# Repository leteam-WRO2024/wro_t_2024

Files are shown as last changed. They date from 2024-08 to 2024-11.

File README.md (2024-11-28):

# Engineering materials

This repository contains engineering materials of "yatta-team (Leteam)" self-driven vehicle's model participating in the WRO Future Engineers competition in the season 2024.

## Content

-   `t-photos` contains photos of the team
-   `v-photos` contains photos of the vehicle
-   `video` contains the video.md file with the link to a video where driving demonstration exists
-   `schemes` contains diagrams about the design and cricut
-   `src` contains the source code that is used
-   `chasis` contains photos of the used chasis and its parts

**AS OF THIS COMMIT IT ONLY CONTAINS THE SOURCE**

## Hardware

| HARDWARE PARTS | References |
| --- | --- |
| Chasis | [4WDRC Chassis S3003 Servo](https://www.elecrow.com/4wd-smart-car-robot-chassis-for-arduino-servo-steering.html) |
| Servo | [S3003 FUTABA SERVO](https://www.es.co.th/schemetic/pdf/et-servo-s3003.pdf) |
| Main-Controller | [RPI-5](https://www.raspberrypi.com/products/raspberry-pi-5/) |
| Secondry-Controller | [Arduino ATmega328p (Arduino Nano 3.x)](https://store.arduino.cc/products/arduino-nano) |
| gyroscope | [BNO085](https://www.ceva-ip.com/wp-content/uploads/2019/10/BNO080_085-Datasheet.pdf) |
| Camera | [usb 170 degree fisheye cam](https://www.amazon.com/ALPCAM-Camera-Module-Webcam-Fisheye/dp/B07VVH39DC/) |
| Other-Parts | Ultrasonics, full-bridge, Voltage regulator, green-light, button |

# Software

We are using the rasberry-pi-4 as a the main controller // computer.
We also use the arduino ATmega328p to - read the Ultrasonic sensors -> filter the readings -> send them using the serial connection to rpi

## Code basic idea

We took advantage of our rasberry pi ability to run multiple processes at the same time so we devided the main program into seperate threads

### MAIN-THREAD

In the main thread we run all the other threads while waiting for the mpu6050 to calibrate, then the main thread waits for a button click after the calibration is finished, our main thread continous to start the car movment by calling the moving function and turning function when needed

---

When the MPU-THREAD finishes calibration and the current angle is set to 0, the main thread waits for a button click.

if the button is clicked the main thread starts the car moving function.

### MPU-THREAD

In the MPU thread we run a function that calculates all the possible angles and calibrates the gyroscope to the current position and then it runs a while loop the gets the current angle by storing it in a class attribute.

-   This thread is a BLOCKING thread, because it blocks the execution of the main thread and that is needed to make the gyroscope calibrate correctly since the gyro we have can not save old calibration like other gyroscopes.

-   The main thread is blocked by a while loop that waits for the current angle to change from -1 to anything else (in this case it should be 0 because after the calibration of the mpu6050 the first angle is set to 0)

-   This thread then keeps running and reading the new angle and setting it to the current angle

-   Events -> None

### DISTANCE-THREAD

In the DISTANCE thread we run a loop that reads the serial continuously, when the arduino finishes reading the ultrasonics, it sends the data throught the serial and the rasberry pi throught this thread it reads and updates the distances.

-   Events -> stop_event which is called at the exit of the program to free and make sure the memory is clean to help pythons garbage collector and stop any overflows

### COLOR-THREAD - direction detection

In the COLOR thread we start reading frames from the camera and do some python and opencv processing on the frames and check for orange and blue colors ... if blue is found then it sets the turn direction to 1 else if orange is found it sets the turn direction to -1 else if orange nor blue were found then turn based on the left or right distance

-> direction-detection chart:
process camera frames -> blue is found <-> direction = 1 <-> else if orange is found <-> direction = -1 <-> else orange nor blue were found -> read left and right distance -> if left is bigger -> direction = 1 <-> else if right is bigger <-> direction = -1

-   Events -> stop_event which stops the thread in a certain case is met and when the program exits

## Turning:

Using ultrasonic sensors (sonar sensors) we check for the right, left, and front distances then we use certain conditions in the moving function that tells the robot to turn based on the direction that was defined by the [COLOR-THREAD](#color-thread---direction-detection).

The turning mechanism uses the mpu6050 to read the current angle and the desired angle to make the robot turn 90 degrees (somewhat exactly ...)

## Avoiding Walls:

Using the right, left distances from the ultrasonics, we calculate a distance error based on a threshold value, then we use a PID algorithm and get a negative or positive return value based on the error ...

After that we use the desired angle (the heading angle e.g 90, 180, 270, 360 or (0)) and the current angle that the gyroscope is reading to calculate an angle error and with some maths we make the robot get the required servo angle to make it go in a 90 degree straight path

we sum the values e.g if the distance error was negative then it helps go away from the right wall, otherwise if positive it helps go away from the left wall, while keeping the angle straight

In the last code, we replaced the readings from ultrasonic sensors with the x values of the black color contours on the right and left sides of the cropped image.

## 3 LAPS detection

At first the robot only runs a for loop for each lap and a for loop inside of it for each corner, and runs the moving and turning functions inside, which works correctly but, we are aware its error prone, In the latest update, we handled each edge of the track with a dedicated function that identifies the end of the edge in the first round when it detects the black color in front of it. In the second round, it identifies the end by the color of the line on the floor, considering the possibility of seeing the black color on the sides while trying to avoid obstacles as the end of the path.

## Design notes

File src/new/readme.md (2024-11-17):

that folder contains our work after removing the ultrasonic sensor from our robot

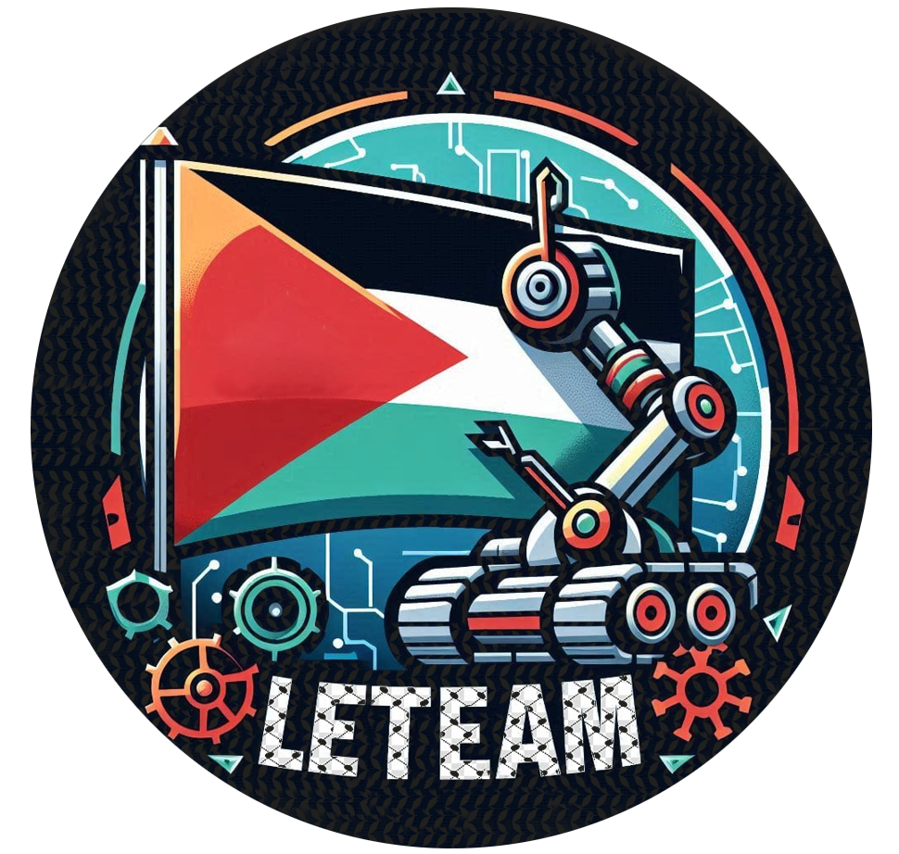
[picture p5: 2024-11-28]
leteam4(1).png

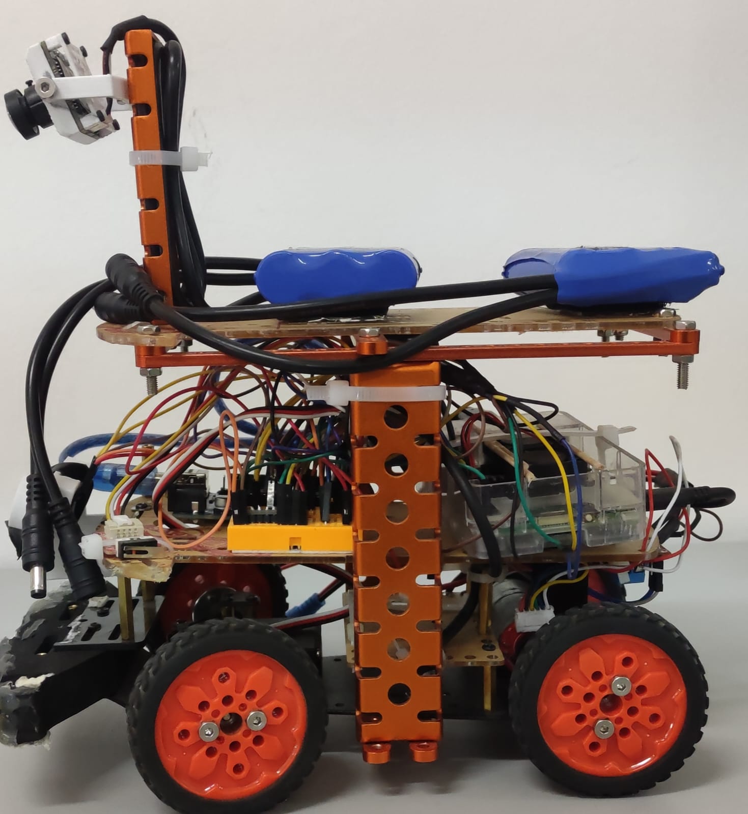
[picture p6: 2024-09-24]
v-photos/left.jpeg

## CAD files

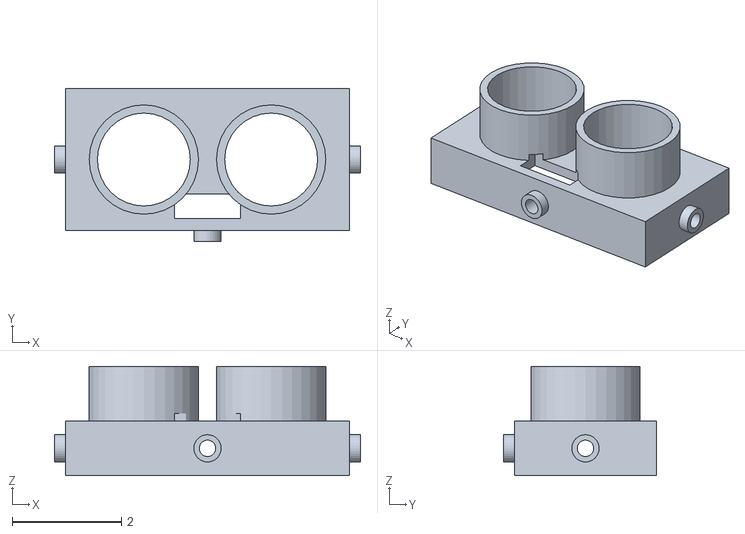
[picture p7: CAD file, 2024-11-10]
models/US100.stl
5.60 x 2.80 x 2.00

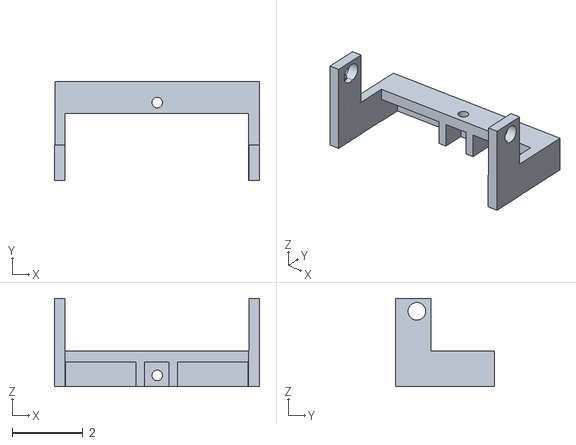
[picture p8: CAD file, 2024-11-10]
models/us100mount.stl
5.81 x 2.80 x 2.50

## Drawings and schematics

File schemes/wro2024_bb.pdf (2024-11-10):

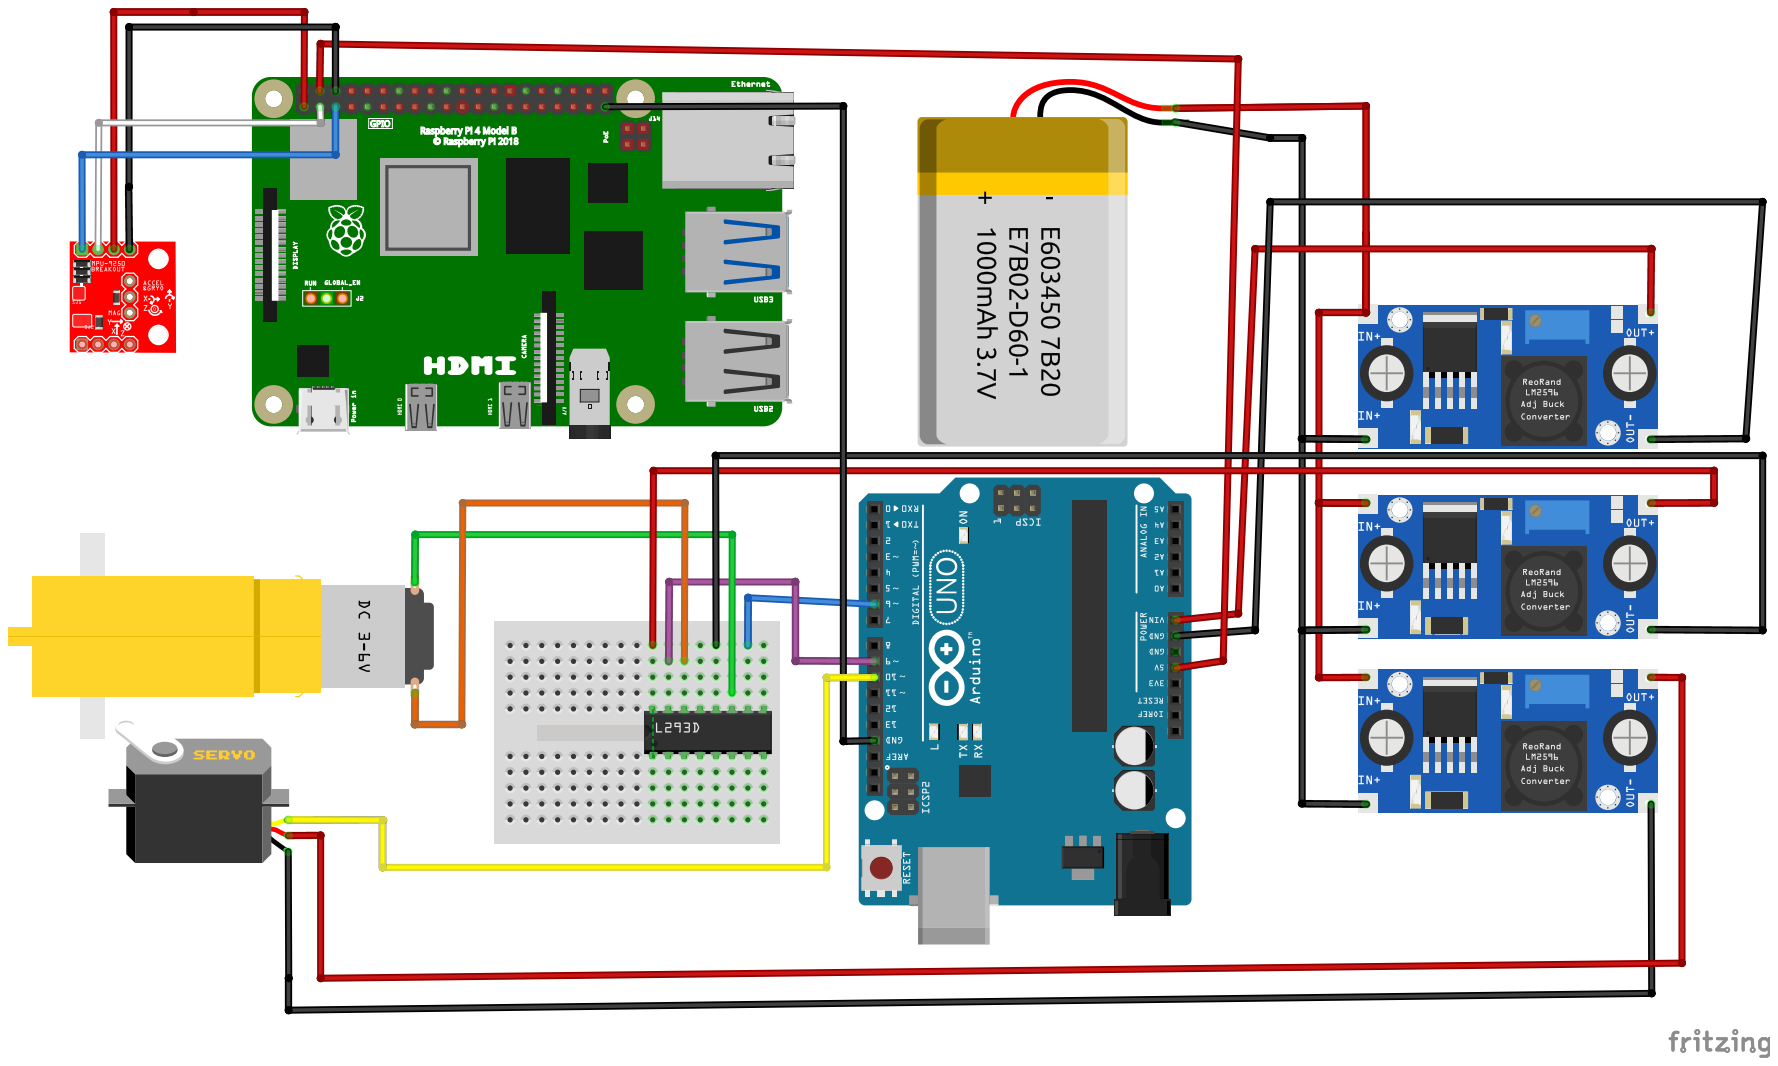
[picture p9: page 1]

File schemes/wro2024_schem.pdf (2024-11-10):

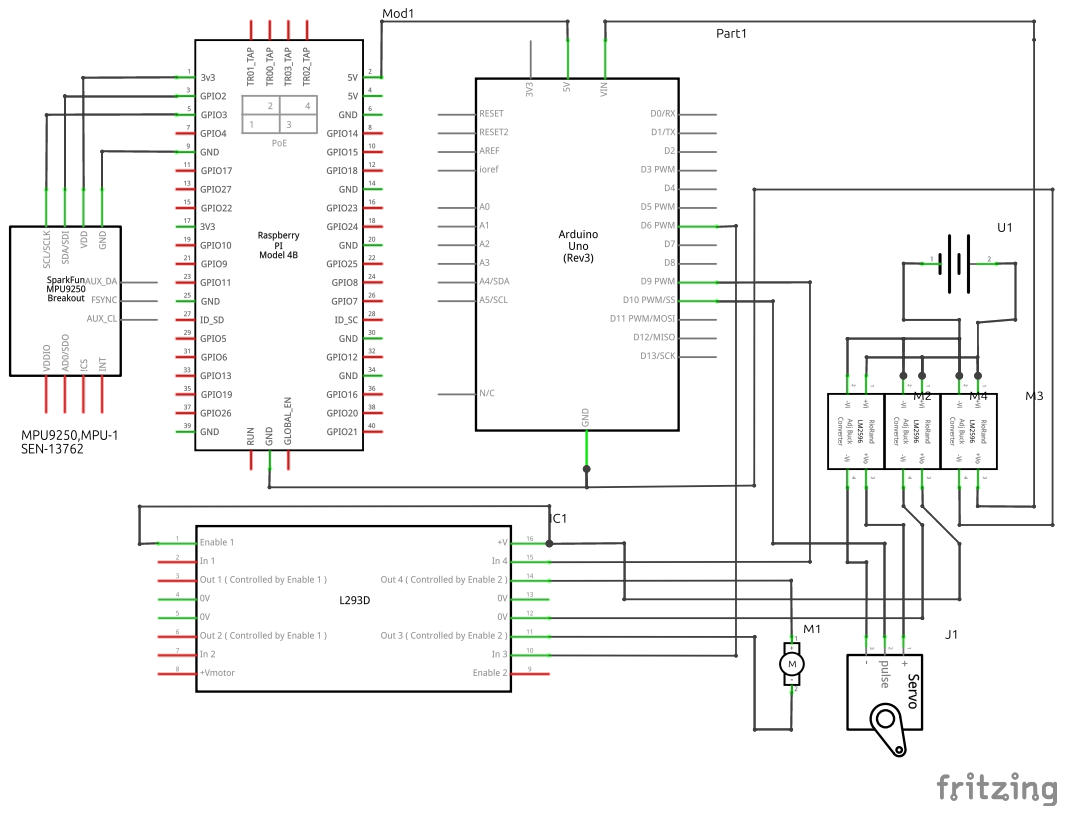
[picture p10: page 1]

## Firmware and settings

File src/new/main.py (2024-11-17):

import imutils
import time
import cv2
import numpy as np
from WebcamVideoStream import WebcamVideoStream as ws
from threading import Thread
from MyGyro import BNO085 as BN
from gpiozero import RotaryEncoder
from threading import Event
import RPi.GPIO as gpo
gpo.setmode(gpo.BCM)
from time import sleep
btn=6
gpo.setup(btn,gpo.IN)
import serial
#initialize arduino communications
ser = serial.Serial('/dev/ttyACM0', 2000000)
ser.flush()
first_Side=True
ser.reset_input_buffer()
time.sleep(2)
if not ser.is_open:
    ser.open()
    time.sleep(2)
#initialize Encoder
rotor = RotaryEncoder(19, 13, wrap=True, max_steps=18000)
rotor.steps = 0
done = Event()
CW=-1

def stop_script():
    print('Exiting')
    done.set()
    
#parameters
min_angle=30
mid_angle=90
max_angle=130
class ColorsCoordinations:

    # allow the camera to warmup
    x=y=w=h=-1
    g_l=[54,98,35]
    g_u=[86,255,255]
    b_l=[0,0,0]
    b_u=[255,255,30]
    bu_l=[110,85,100]
    bu_u=[125,255,255]
    r_l=[170,50,73]
    r_u=[180,255,255]
    o_l=[0,100,110]
    o_u=[50,255,255]
    #Ignore the warning message
    cam=ws()
    cam.start()
    xr=-1
    yr=-1
    xl=-1
    yl=-1
    yf=-1
    xo=-1
    xb=-1
    imu=BN()
    imu.start()
    def getcoor(self,imageFrame,l,u,name,delay,show,minsize):
        while True:

            hsv_frame2 = cv2.cvtColor(imageFrame, cv2.COLOR_BGR2HSV)
            kernal = np.ones((5, 5), "uint8") 
            dilated_frame = cv2.dilate(hsv_frame2, kernal)
            dilated_frame = cv2.erode(dilated_frame, kernal)

            lower = np.array([l[0], l[1], l[2]], np.uint8) 
            upper = np.array([u[0], u[1], u[2]], np.uint8) 
            mask = cv2.inRange(dilated_frame, lower, upper) 

            contours, _ = cv2.findContours(mask, cv2.RETR_TREE, cv2.CHAIN_APPROX_NONE)
            if len(contours)>0:
                c = max(contours, key = cv2.contourArea)
                area = cv2.contourArea(c)
                if(area > minsize):
                    cv2.drawContours(imageFrame, c, -1, (0, 255, 0), 2)
                    self.x, self.y, self.w, self.h = cv2.boundingRect(c)

        
            x=self.x 
            y=self.y
            w=self.w
            h=self.h
            self.x=self.y=-1
            if show:
                cv2.imshow(name,imageFrame)
                key = cv2.waitKey(delay) & 0xFF
            return x,y,w,h
    def boarders(self,delay,show):
        frame=self.cam.read()
        #print(frame.shape)
        #frame1=frame
        frame1=frame[420:450,0:400]
        frame2=frame[420:450,400:800]
        #show fps
        '''
        nframe=time.time()
        fps=1/(nframe-pframe)
        pframe=nframe
        fps=int(fps)
        fps=str(fps)
        cv2.putText(frame2,fps,(7,25),cv2.FONT_HERSHEY_SIMPLEX,1,(255,255,255),1,cv2.LINE_AA)
        '''
        xl, self.yl, lw, lh=c.getcoor(frame1,c.b_l,c.b_u,"f1",delay,show,300)
        
        if xl != -1:
            self.xl = (xl + lw) // 2
        else:
            self.xl = -1
        
        self.xr, self.yr, rw, rh=c.getcoor(frame2,c.b_l,c.b_u,"f2",delay,show,300)
        
    def front(self,delay,show,heading):
        frame=self.cam.read()

        curr=self.imu.Read_Yaw()
        while curr=='err':
            curr=self.imu.Read_Yaw()
        diff=heading-curr
        #print(diff)
        if diff>300:
            diff=360-diff
        elif diff<-300:
            diff=diff+360
            
        #print(diff)
        diff=int(diff)*4
        if diff>300:
            diff=300
        elif diff<-300:
            diff=-300
        
        frame3=frame[90:450,350+diff:450+diff]

        x3,y3,w,h=c.getcoor(frame3,c.b_l,c.b_u,"f3",delay,show,1000)
        #print(y3)
        self.yf=y3
    def ground(self,delay,show,heading):
        #pframe=time.time()
        frame=self.cam.read()


        
        frame3=frame[150:225,380:420]

        self.xb,y1,w,h=c.getcoor(frame3,c.bu_l,c.bu_u,"f_blue",delay,show,50)
        self.xo,y2,w,h=c.getcoor(frame3,c.o_l,c.o_u,"f_orange",delay,show,50)        
        


c=ColorsCoordinations()
frame=c.cam.read()

time.sleep(0.1)
pframe=0
nframe=0
show=False
delay=5
side_values=[]
def turn90_halfback():
    rotor.steps=0
    speed=200
    stop()
    roter_limmit=280
    go_left(speed)
    #while rotor.steps<roter_limmit:
        #ser.write(code.encode("utf-8"))
        #time.sleep(0.1)
    while  rotor.steps< roter_limmit:
        forward(speed)
    stop()

    go_right(speed)
    time.sleep(0.2)
    while  rotor.steps> roter_limmit:
        backward(speed)
    stop()
    time.sleep(0.2)
def turn90():
    rotor.steps=0
    speed=200
    stop()
    roter_limmit=470
    go_left(speed)
    #while rotor.steps<roter_limmit:
        #ser.write(code.encode("utf-8"))
        #time.sleep(0.1)
    while  rotor.steps< roter_limmit:
        forward(speed)
    stop()
def turn90c():
    rotor.steps=0
    speed=200
    stop()
    roter_limmit=470
    go_right(speed)
    #while rotor.steps<roter_limmit:
        #ser.write(code.encode("utf-8"))
        #time.sleep(0.1)
    while  rotor.steps< roter_limmit:
        forward(speed)
    stop()

def calculate_sides_values(first_side):
    side_values.append(first_side)
    for i in range(3):
        next_side_angle=side_values[i]+90
        if next_side_angle>360:
            next_side_angle=next_side_angle-360
        side_values.append(next_side_angle)
    print(side_values)
#communications with arduino test code
def forward(speed):
    code = f"f:{speed}$"    
    ser.write(code.encode("utf-8"))
def backward(speed):
    code = f"b:{speed}$"    
    ser.write(code.encode("utf-8"))
def stop():
    code = f"s: $"    
    ser.write(code.encode("utf-8"))
def set_servo_angle(angle):
    code = f"a:{angle}$"
    ser.write(code.encode("utf-8"))
def go_right(speed):
    set_servo_angle(max_angle)
    forward(speed)
def go_left(speed):
    print("am going left")
    set_servo_angle(min_angle)
    forward(speed)
def go_right_r(speed):
    set_servo_angle(min_angle)
    backward(speed)
def go_left_r(speed):
    set_servo_angle(max_angle)
    backward(speed)
def lastrun(side_angle):

    rotor.steps=0
    code = f"a:{mid_angle}$"
    ser.write(code.encode("utf-8"))
    speed=255
    while rotor.steps<500:
        speed_offset=0#int((rotor.steps/900)*80)
        speed=speed-speed_offset
        if speed<180:
            speed=180
        code = f"f:{speed}$"    
        ser.write(code.encode("utf-8"))
        err=0
        Gyro_angle=c.imu.Read_Yaw()
        if not Gyro_angle=="err":
            err=(side_angle-Gyro_angle)
            if err>100:
                err=360-err
            elif err<-100:
                err=err+360
        servo_angle=mid_angle+err
        code = f"a:{servo_angle}$"
        ser.write(code.encode("utf-8"))
        c.boarders(delay,show)
        
    code = f"s:{speed}$"    
    ser.write(code.encode("utf-8"))
    print(rotor.steps)
    
def onesidedrive(side_angle):
    global first_Side
    global CW
    c.front(delay,show,side_angle)
    roter_limit=1200
    if first_Side:
        first_Side=False
        roter_limit=50
    c.boarders(delay,show)
    rotor.steps=0
    yf=c.yf
    code = f"a:{mid_angle}$"
    ser.write(code.encode("utf-8"))
    speed=255
    ptime=time.time()
    while yf==-1 or rotor.steps<roter_limit:
        speed_offset=0#int((rotor.steps/900)*80)
        speed=speed-speed_offset
        if speed<180:
            speed=180
        code = f"f:{speed}$"    
        ser.write(code.encode("utf-8"))
        err = 0
        Gyro_angle = c.imu.Read_Yaw()
        
        dist_err = 0
        
        if c.xl > 70 and c.xl != -1:
            dist_err = -(70 - c.xl) * 15
        elif c.xr < 200 and c.xr != -1:
            #print("am here")
            dist_err = -(200 - c.xr) * 4
            
        if not Gyro_angle=="err":
            err=(side_angle-Gyro_angle)
            if err>100:
                err=360-err
            elif err<-100:
                err=err+360

        servo_angle = mid_angle + err + dist_err

        code = f"a:{servo_angle}$"
        ser.write(code.encode("utf-8"))
        c.boarders(delay,show)
        c.front(delay,show,side_angle)
        yf=c.yf
        ftime=time.time()
        fps=1/(ftime-ptime)
        ptime=ftime
        #print(f"fps: {fps} {c.xr}{c.xl}")
        
    code = f"s:{speed}$"    
    ser.write(code.encode("utf-8"))
    print(rotor.steps)
def ccw_run():

    for i in range(3):
        onesidedrive(side_values[0])
        turn90()
        onesidedrive(side_values[3])
        turn90()
        onesidedrive(side_values[2])
        turn90()
        onesidedrive(side_values[1])
        turn90()
    lastrun(side_values[0])
    print(time.time()-t1)
    
def cw_run():

    for i in range(3):
        onesidedrive(side_values[0])
        turn90c()
        onesidedrive(side_values[1])
        turn90c()
        onesidedrive(side_values[2])
        turn90c()
        onesidedrive(side_values[3])
        turn90c()
    lastrun(side_values[0])
    print(time.time()-t1)
    
def firstsidedrive(side_angle):
    global first_Side
    global CW
    c.front(delay,show,side_angle)
    roter_limit=1200
    if first_Side:
        first_Side=False
        roter_limit=500
    c.boarders(delay,show)
    c.ground(delay,show,side_angle)
    rotor.steps=0
    yf=c.yf
    code = f"a:{mid_angle}$"
    ser.write(code.encode("utf-8"))
    speed=100
    ptime=time.time()
    while c.xo==-1 and c.xb==-1:
        c.ground(delay,show,side_angle)
        speed_offset=0#int((rotor.steps/900)*80)
        speed=speed-speed_offset
        if speed<180:
            speed=180
        code = f"f:{speed}$"    
        ser.write(code.encode("utf-8"))
        err=0
        Gyro_angle=c.imu.Read_Yaw()
 
        if not Gyro_angle=="err":
            err=(side_angle-Gyro_angle)
            if err>100:
                err=360-err
            elif err<-100:
                err=err+360
        print(f"err {err}")
        servo_angle=mid_angle+err
        code = f"a:{servo_angle}$"
        ser.write(code.encode("utf-8"))
        c.boarders(delay,show)
        c.front(delay,show,side_angle)
        yf=c.yf
        ftime=time.time()
        fps=1/(ftime-ptime)
        ptime=ftime
        #print(f"fps: {fps} {c.xr}{c.xl}")
    if c.xo==-1:
        print("CCW")
        CW=False
    else:
        print("CW")
        CW=True

    code = f"s:{speed}$"    
    ser.write(code.encode("utf-8"))
    print(rotor.steps)


while True:
    if not gpo.input(btn):
        time.sleep(1)
        t1=time.time()
        heading=c.imu.Read_Yaw()
        while heading=='err':
           heading=c.imu.Read_Yaw()
        calculate_sides_values(heading)



        firstsidedrive(heading)

        first_Side=True

        if CW:
            cw_run()
        else:
            print("am in ccw")
            ccw_run()

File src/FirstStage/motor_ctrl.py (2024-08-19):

from gpiozero import Motor, AngularServo
from gpiozero.pins.pigpio import PiGPIOFactory
from typing import Union, NewType
from time import sleep
from pid_ctrl import pidc


class mctrl():
    def __init__(self, motorPins: list, servoPin: int, speed: int = 1, debug: bool = False) -> None:
        self.motorPins: list = motorPins
        self.servoPin: int = servoPin

        # OLD pidc vals: 0.6, 0.0, 0.3 True
        self.motor: Motor = Motor(*self.motorPins)
        self.factory = PiGPIOFactory()
        self.servo = AngularServo(self.servoPin, min_angle=0, max_angle=180,min_pulse_width=0.0005, max_pulse_width=0.0025, pin_factory=self.factory)

        # 0.8789 0.04 0.048
        # self.pid = pidc(0.6, 0.038, 0.034, True)
        self.pid = pidc(0.9, 0, 0.02, True)

        self.distance_threshold = 25
        self.debug = debug

        self.__speed = speed
        self.__direction = 0

        self.min_angle = 60
        self.max_angle = 140
        self.mid_angle = 110
        
        self.turns = 0

    @property
    def angle(self):
        return self.servo.angle

    @angle.setter
    def angle(self, val):
        self.servo.angle = self.map_angle(val)

    @property
    def direction(self):
        return self.__direction

    @direction.setter
    def direction(self, val):
        if val not in [1, 0, -1]:
            self.__direction = 0
            print("Direction should be in [1, 0, -1] ... Resseting to 0")
        self.__direction = val

    @property
    def speed(self):
        return self.__speed

    @speed.setter
    def speed(self, val):
        self.__speed = round(min(1, max(0, val)), 2)

    def minfo(self, val):
        if self.debug:
            print(val)

    def get_next_angle(self, angle: Union[int, float], ninety_deg: bool = False):
        next_angle = ((angle + 10) + (self.direction * 90)) % 360
        if ninety_deg:
            next_angle = (round(next_angle / 90)) * 90

        return next_angle

    def get_heading_angle(self, angle: Union[float, int]):
        return (self.get_next_angle(angle, True) - (self.direction * 90)) % 360
    
    def get_current_turn(self, angle: Union[float, int]):
        if self.get_heading_angle(angle = angle) == 0:
            self.turns += 1
            
    def map_angle(self, angle: Union[int, float]):
        return max(self.min_angle, min(self.max_angle, angle))

    def adjust_angle(self, heading: Union[int, float], reading: Union[int, float], right_distance: Union[int, float], left_distance: Union[int, float]):


        if right_distance == 0:
            right_distance = 200
        if left_distance == 0:
            left_distance = 200
        
        distance_error = min(right_distance, 40) - min(left_distance, 40)
        
    
        error_val = reading - heading + distance_error
        error_val = ((error_val + 180) % 360) - 180
        self.angle = (error_val + self.mid_angle)

    def direction_turn(self):
        if self.direction == -1:
            self.turn_right()
        elif self.direction == 1:
            self.turn_left()

    # Needs more work i think never tested it fully
    def fix_forward(self, heading: Union[float, int] = 0, reading: Union[float, int] = 0, left_distance: Union[float, int] = 0, right_distance: Union[float, int] = 0):
        print("\n\n::::::::Inside fix, forward::::::::\n\n")

        if left_distance > right_distance:
            self.turn_right()
        elif right_distance > left_distance:
            self.turn_left()

        self.move_backward(nspeed=1)
        sleep(1)
        self.reverse_angle()
        self.move_forward(nspeed=0.8)
        sleep(0.84)
        for _ in range(3):
            self.adjust_angle(heading, reading, left_distance, right_distance)
            sleep(0.005)

    def fix_stuck(self, heading: Union[float, int] = 0, reading: Union[float, int] = 0, left_distance: Union[float, int] = 0, right_distance: Union[float, int] = 0):
        self.stop_car()
        self.reverse_angle()
        self.move_backward(nspeed=1)
        sleep(1)
        self.reverse_angle()
        self.move_forward()

    def reverse_angle(self):
        self.angle = (self.mid_angle - self.angle) + self.mid_angle

    def turn_forward(self):
        self.angle = self.mid_angle

    def turn_left(self):
        self.angle = self.min_angle

    def turn_right(self):
        self.angle = self.max_angle

    def move_forward(self, nspeed: Union[int, float]  = 0):
        self.motor.forward(nspeed if nspeed else self.speed)

    def move_backward(self, nspeed: Union[int, float] = 0):
        self.motor.backward(nspeed if nspeed else self.speed)

    def stop_car(self):
        self.motor.stop()

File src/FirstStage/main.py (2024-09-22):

from ultrasonic_ctrl import ultra
from mpu_ctrl import MPU
from encoder import Encoder
from gpiozero import Button, LED
from motor_ctrl import mctrl
from time import sleep, time
from threading import Thread, Event
from ColorCoords import ColorsCoordinations
import cv2
import numpy as np

new_J = 0
COLOR_RANGES = {
    "green":    (np.array([55, 173, 35], np.uint8), np.array([90, 255, 205], np.uint8)),
    "red":      (np.array([0, 51, 64], np.uint8), np.array([180, 255, 255], np.uint8)),
    "orange":   (np.array([2, 40, 60], np.uint8), np.array([30, 255, 255], np.uint8)),
    "blue":     (np.array([90, 105, 90], np.uint8), np.array([125, 255, 255], np.uint8))
}

def read_ultra(event: Event):
    while not event.is_set():
        frontUltra.distance = frontUltra.calcDistance()
        leftUltra.distance = leftUltra.calcDistance()
        rightUltra.distance = rightUltra.calcDistance()

def mpu_loop(mpu: MPU):
    global new_J
    mpu.setUp()
    mpu.calibrateGyro(500)

    while True:
        try:
            mpu.currentAngle = mpu.compFilter(1) + ((3 * new_J) * motors.direction)
            # mpu.currentAngle = mpu.compFilter(1)
            sleep(0.000007)
        except:
            
            pass

def get_color(event: Event):
    motors.direction = 0
    while not event.is_set():
        orange = color_reco.detect_color("orange")
        blue = color_reco.detect_color("blue")
        if orange != (-1, -1):
            motors.direction = -1
        elif blue != (-1, -1):
            motors.direction = 1

        if motors.direction != 0:
            event.set()
            color_reco.stop = True
        # print(f"direction: {motors.direction}")


def starting_point_adjustment():
    heading = motors.get_heading_angle(mpu.currentAngle)
    motors.move_forward(0.7)


    if frontUltra == 0:
        sleep(1)
    elif frontUltra > 145:
        while (frontUltra > 145 or frontUltra == 0):
            pass
        # motors.adjust_angle(heading, mpu.currentAngle, rightUltra, leftUltra)
            # print("adjusting")
    print("out")

    motors.stop_car()
    motors.turn_forward()


def moveUntilDist():
    heading = motors.get_heading_angle(mpu.currentAngle)
    motors.adjust_angle(heading, mpu.currentAngle, rightUltra, leftUltra)

    motors.move_forward()

    motors.minfo(f"\n\nFRONT:: {frontUltra}\n\n")
    while True:
            # print(f"Moving with speed {motors.speed}  --- front {frontUltra}")
        if (frontUltra < 82 and frontUltra != 0) or (leftUltra > 120 or rightUltra > 120):
            break
        motors.adjust_angle(heading, mpu.currentAngle, rightUltra, leftUltra)
                
        motors.minfo(
            f"\nFRONT:: {frontUltra}\nRIGHT:: {rightUltra}\nLEFT:: {leftUltra}\n")

    print("OUT OF LOOP")
    motors.turn_forward()
    motors.stop_car()
    motors.speed = 1
    
def turn():

    heading = motors.get_heading_angle(mpu.currentAngle)

    mpu.nextAngle = motors.get_next_angle(heading, True)
    motors.direction_turn()
    sleep(0.003)
     
    motors.move_forward(1)

    mpu.dinfo(
        f"ABOVE:: ({mpu.currentAngle} - {mpu.nextAngle}) * {motors.direction} = {(mpu.nextAngle - mpu.currentAngle) * motors.direction}")
    
    while not (250 > (mpu.currentAngle - mpu.nextAngle) * motors.direction >= -5):
        mpu.dinfo(
            f"({mpu.currentAngle} - {mpu.nextAngle}) * {motors.direction} = {(mpu.nextAngle - mpu.currentAngle) * motors.direction}")
        sleep(0.00005)
        

    mpu.dinfo(
        f"UNDER:: ({mpu.currentAngle} - {mpu.nextAngle}) * {motors.direction} = {(mpu.nextAngle - mpu.currentAngle) * motors.direction}")

    motors.turn_forward()
    motors.stop_car()
    sleep(0.36)

def main():
    global new_J
    # start_sleep = 0.44

    motors.turn_forward()
    motors.speed = 1
    
    color_event = Event()
    dist_event = Event()

    Thread(target=mpu_loop, args=(mpu, )).start()

    ready = mpu.isReady()

    Thread(target=get_color, args=(color_event, )).start()
    Thread(target=read_ultra, args=(dist_event, )).start()

    # while not btn.is_active:
    #     sleep(0.1)

    while motors.turns < 3:
        moveUntilDist()
        # sleep(start_sleep)
        turn()
        motors.get_current_turn(mpu.currentAngle)
        sleep(0.1)
        # print(f"Turns: {motors.turns}")
        new_J = new_J + 1
    
    print("Finishing")
    starting_point_adjustment()
    sleep(1)
    dist_event.set()


if __name__ == '__main__':
    new_J = 0

    frontUltra = ultra(10, 26)
    rightUltra = ultra(22, 16)
    leftUltra  = ultra(9, 11)

    debugList = [False, False]

    motors = mctrl(motorPins=[24, 13], servoPin=12, speed=1, debug=debugList[0])
    mpu = MPU(gyro=250, acc=2, tau=0.98, debug=debugList[1])
    enc = Encoder(15)

    color_reco = ColorsCoordinations().start()
    btn = Button(20)

    main()

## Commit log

2024-07-20 Second stage-working yaaaay
2024-07-24 new faster motor for first stage
2024-08-19 raspberry only
2024-09-22 adding other stuff
    [circuit design.fzz]
2024-11-10 Rename schemes/circuit design.fzz to schemes/old/circuit design.fzz
    [circuit design.fzz]
2024-11-28 Add files via upload
    update for final stage code without using ultrasonic sensors in design
